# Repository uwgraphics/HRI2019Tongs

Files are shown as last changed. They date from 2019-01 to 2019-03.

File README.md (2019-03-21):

# Design for the Instrumented Tongs
The repository contains Solidworks model files and .STL files for the design of the Instrumented Tongs.

The Instrumented Tongs are used to record large scale object manipulation tasks performed by human demonstrators. The tongs have __Optitrack motion capture markers__ and __ATIMini40 force-torque sensors__.

## 3D printed parts
* The body of tongs along with the 2 pads are 3D printed.
* Directly use the STL files (upper_arm.stl, lower_arm.stl, switchable_plate.stl) to print them. The units are millimeters.
* Nylon or ABS printed with a Fused Deposition Modeling (FDM) printer is recommended however printing with other plastics is possible. Since the tongs are large, printing with a Stereolithography (SLA) printer may produce slightly warped parts during the curing process.  
* The hole pattern where the force torque sensors mount needs to be accurate so printing with a horizontal orientation is recommended.
* The prongs provided for mounting the motion capture markers need to be threaded. Use M4 x 0.7 (tap)die to thread the prongs.

## Small Parts
* Pin - [M5 x 20mm Dowel Pin](https://www.grainger.com/product/GRAINGER-APPROVED-Unhardened-Ground-Stainless-1TY33)
* Bushings 
1. 1 x [Igus Plain Bush JSM-0507-05](https://www.igus.com/product/?artnr=JSM-0507-05)
1. 2 x [Igus Plain Bush JFM-0507-05](https://www.igus.com/product/?artnr=JFM-0507-05)
* Spring - [General spring available for salad tongs](https://www.webstaurantstore.com/american-metalcraft-fs911-replacement-flat-spring-for-utility-tongs/45935HS.html)
* Screws - Screws required to attach the force torque sensors. 

## Advanced Solidworks Users
To modify the tongs start with the assembly file assembly.SLDASM. Open the corresponding parts from the assembly. The file armV2.SLDPRT is the body of the tongs and has two configurations corresponding to the upper and lower sides of the tongs. Use the [configuration manager](http://help.solidworks.com/2018/english/solidworks/sldworks/c_Configurations_Overview.htm) to switch between configurations.

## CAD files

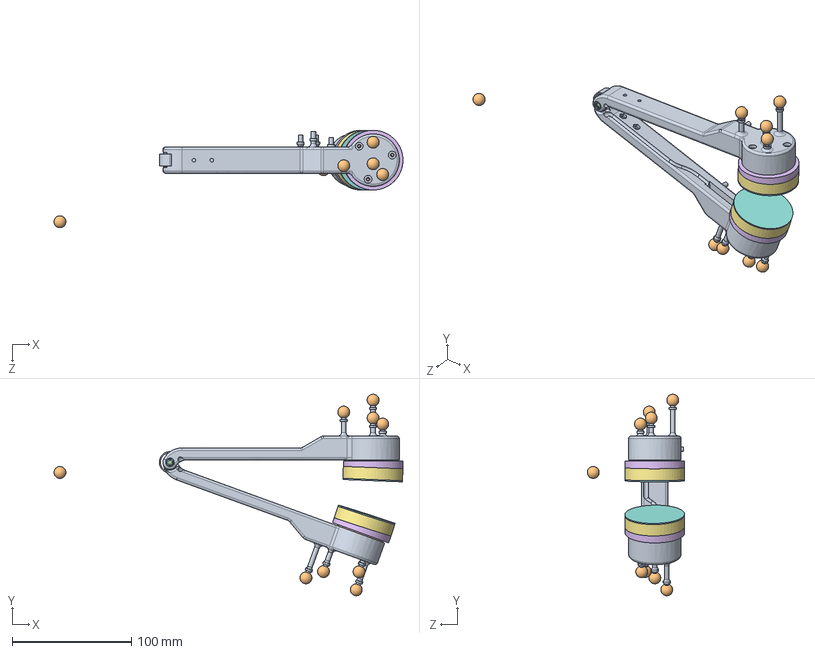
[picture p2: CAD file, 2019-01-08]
solidworks_models/assembly.SLDASM
292.1 x 168.8 x 81.6 mm
armV2 x 2
bushing - JSM - 0507 - 10
bushing - JFM-0507-05 x 2
pin
ATI-Default x 2
switchable_plate x 2
pad_foam1 x 2
pad_foam2 x 2
spring
marker x 8

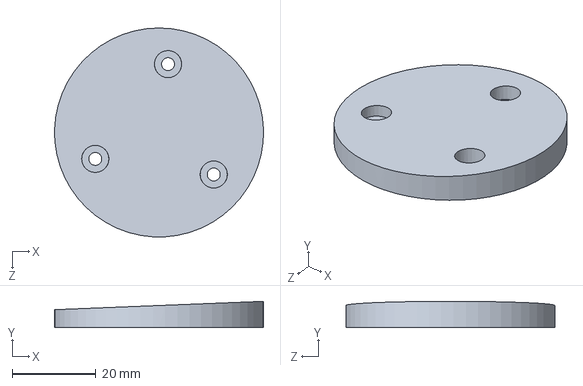
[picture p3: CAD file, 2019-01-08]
solidworks_models/switchable_plate.SLDPRT
50.0 x 6.30 x 50.0 mm

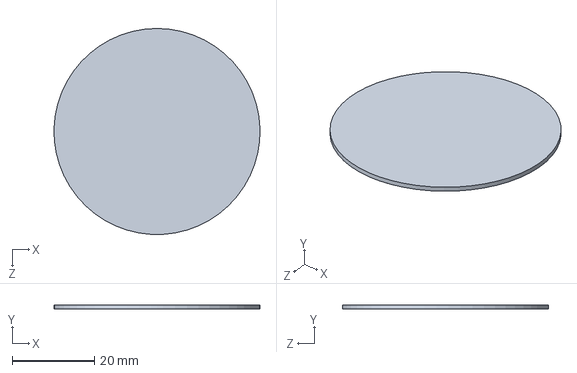
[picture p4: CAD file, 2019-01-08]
solidworks_models/pad_foam2.SLDPRT
50.0 x 1.00 x 50.0 mm

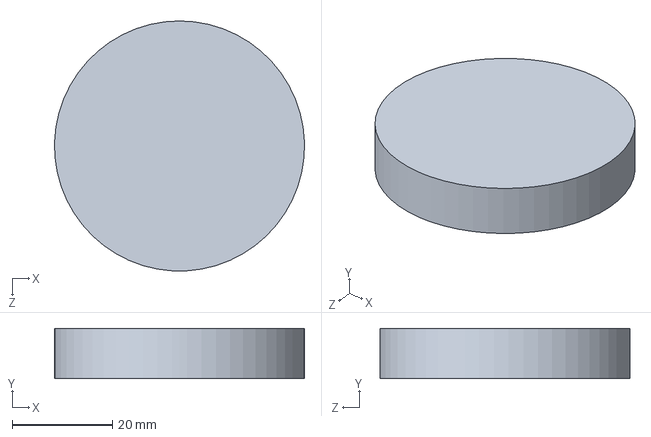
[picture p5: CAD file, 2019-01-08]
solidworks_models/pad_foam1.SLDPRT
50.0 x 10.0 x 50.0 mm

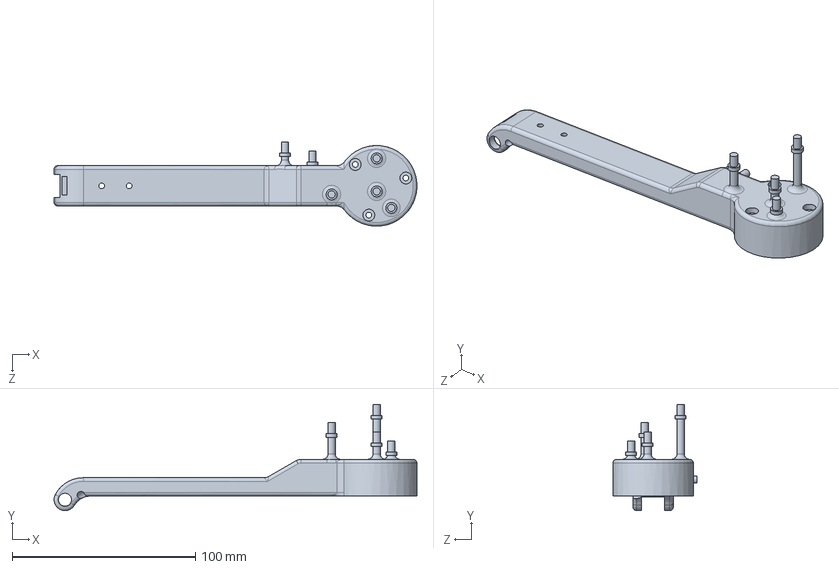
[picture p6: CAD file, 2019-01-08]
solidworks_models/armV2.SLDPRT
198.0 x 58.0 x 46.0 mm

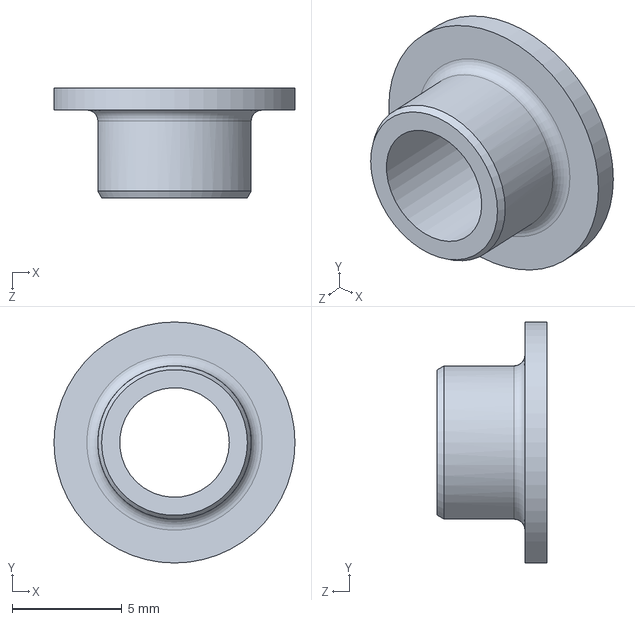
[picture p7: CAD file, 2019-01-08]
solidworks_models/bushing - JFM-0507-05.SLDPRT
11.0 x 11.0 x 5.00 mm

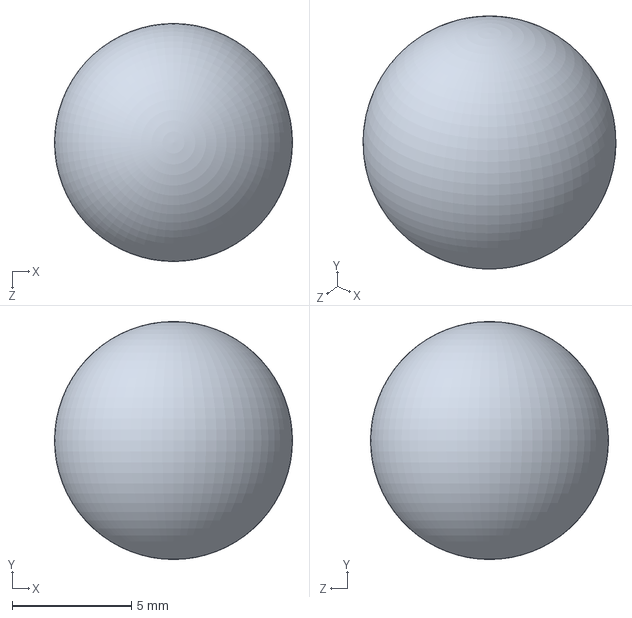
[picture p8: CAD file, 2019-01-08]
solidworks_models/marker.SLDPRT
10.0 x 10.0 x 10.0 mm

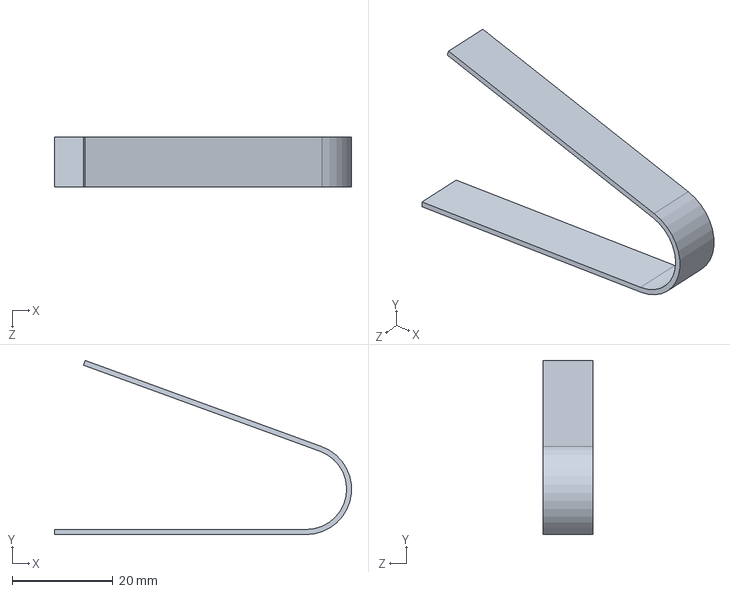
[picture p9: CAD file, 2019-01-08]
solidworks_models/spring.SLDPRT
59.0 x 34.6 x 10.0 mm

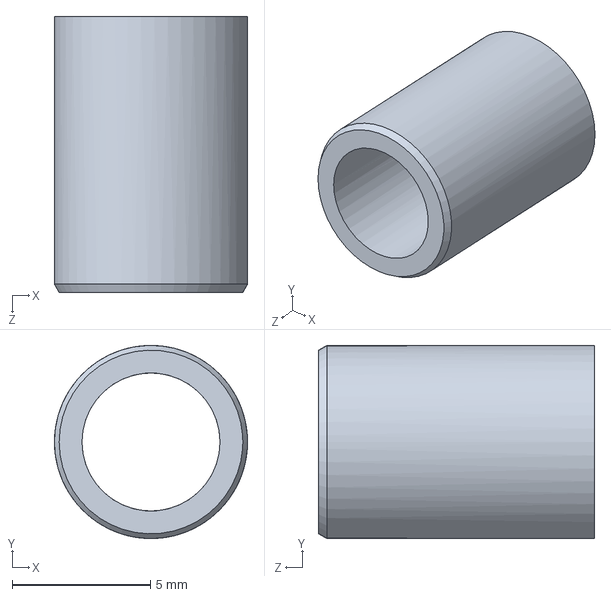
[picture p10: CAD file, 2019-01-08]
solidworks_models/bushing - JSM - 0507 - 10.SLDPRT
7.00 x 7.00 x 10.0 mm

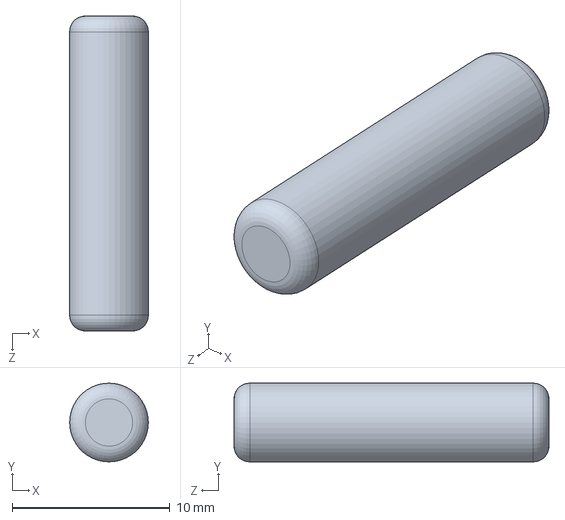
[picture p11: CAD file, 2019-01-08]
solidworks_models/pin.SLDPRT
5.00 x 5.00 x 20.0 mm

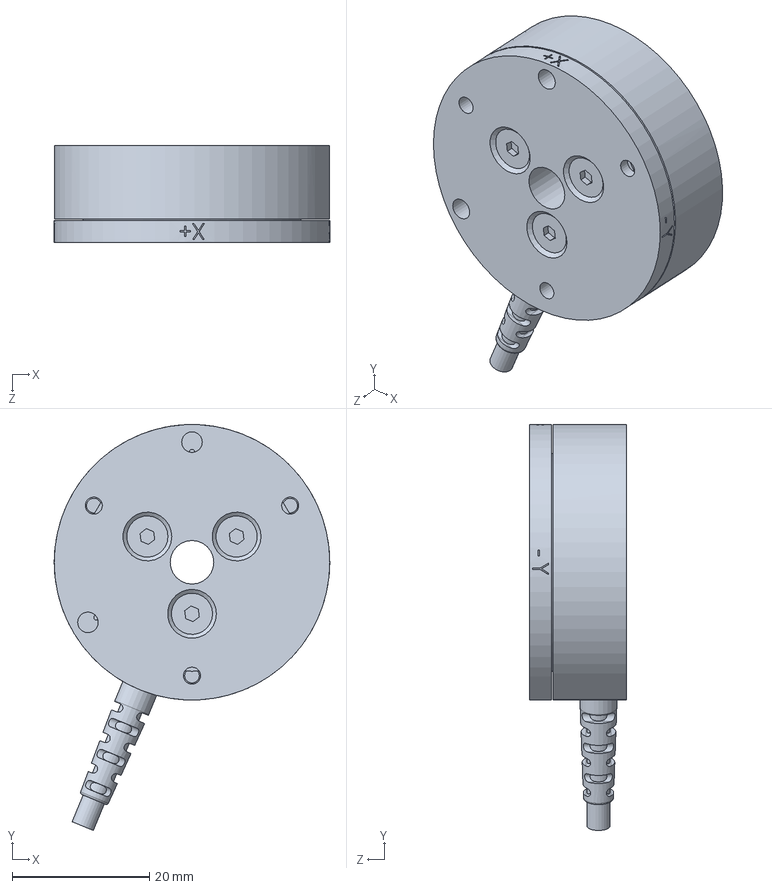
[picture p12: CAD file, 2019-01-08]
solidworks_models/ATI-Default.SLDPRT
40.1 x 59.1 x 14.1 mm

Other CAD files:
stl_models/switchable_plate.STL

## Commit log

2019-01-08 adding files to repo
    [ATI-Default.SLDPRT, armV2.SLDPRT, assembly.SLDASM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]
2019-01-08 renamed folder
    [switchable_plate.STL]
